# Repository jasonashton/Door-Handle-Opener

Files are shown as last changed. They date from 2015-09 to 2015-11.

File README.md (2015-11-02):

# Door-Handle-Opener

Opens a door handle with a Nema 17.  
**Problem:** In our residence hall, we can open the main doors with our ID cards but have to use a key to open the individual rooms.  
**Solution:** We've built a spool-and-motor system to open the door handle without altering the existing door.

##Parts List
1. Custom Built Microcontroller (heavily based on Arduino Uno) <em>see wiki</em>
2. A4988 Motor Driver (allows us to drive motors with independent power supply)
3. Nema 17 Stepper Motor
4. 3D Printed Parts <em>see models</em>

##Configuring the Motor Driver
The Motor Driver we chose to use is the Polulu A4988  
The Motor we chose is a Nema 17

To configure the current limiting on the motor driver, we use the formula
Current Limit = VREF x 2.5

Measure the voltage on the potentiometer (VREF). In Full Step mode, the driver will
only pull 70% of the current.

Current Limit / 2.5 = VREF

To get a full-step coil current of 1.4 Amps, the limit should be 1.4A/0.7 or 2
Amps. To find VREF, 2A/2.5 = .8 Volts. 

However, that might run a bit hot. Anything over 1 Amp requires external
cooling. To achieve a 1 Amp load,
1A/0.7 = 10/7A & 10/7A/2.5 = .572 Volts on VREF

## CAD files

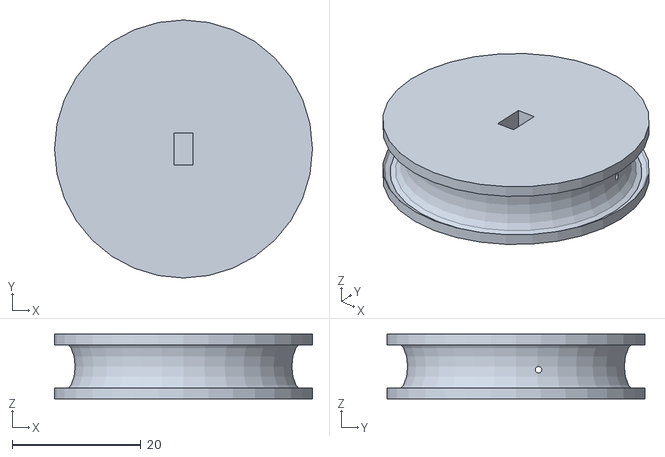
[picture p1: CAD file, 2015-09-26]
models/spool.stl
40.0 x 40.0 x 10.0

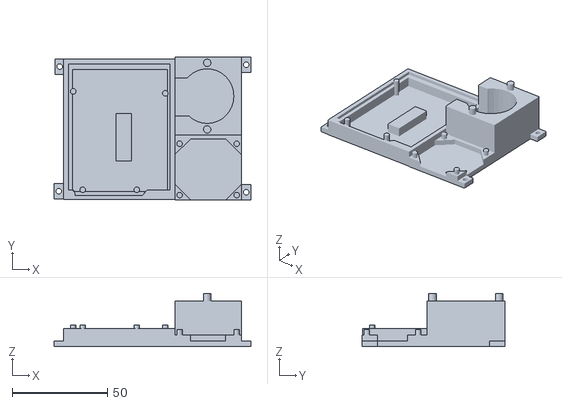
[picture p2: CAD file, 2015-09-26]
models/motorboard_mount.stl
103.5 x 75.0 x 28.0

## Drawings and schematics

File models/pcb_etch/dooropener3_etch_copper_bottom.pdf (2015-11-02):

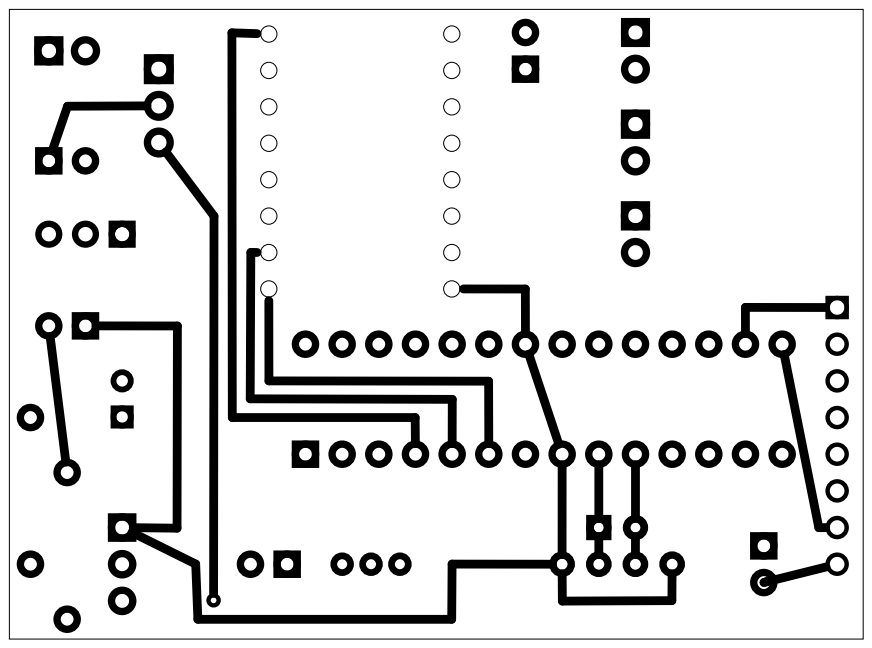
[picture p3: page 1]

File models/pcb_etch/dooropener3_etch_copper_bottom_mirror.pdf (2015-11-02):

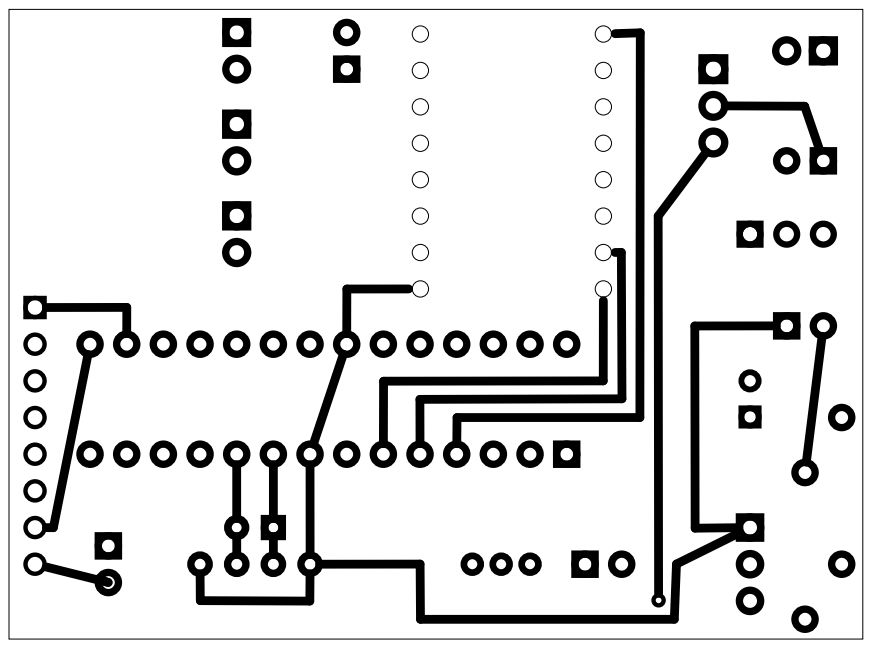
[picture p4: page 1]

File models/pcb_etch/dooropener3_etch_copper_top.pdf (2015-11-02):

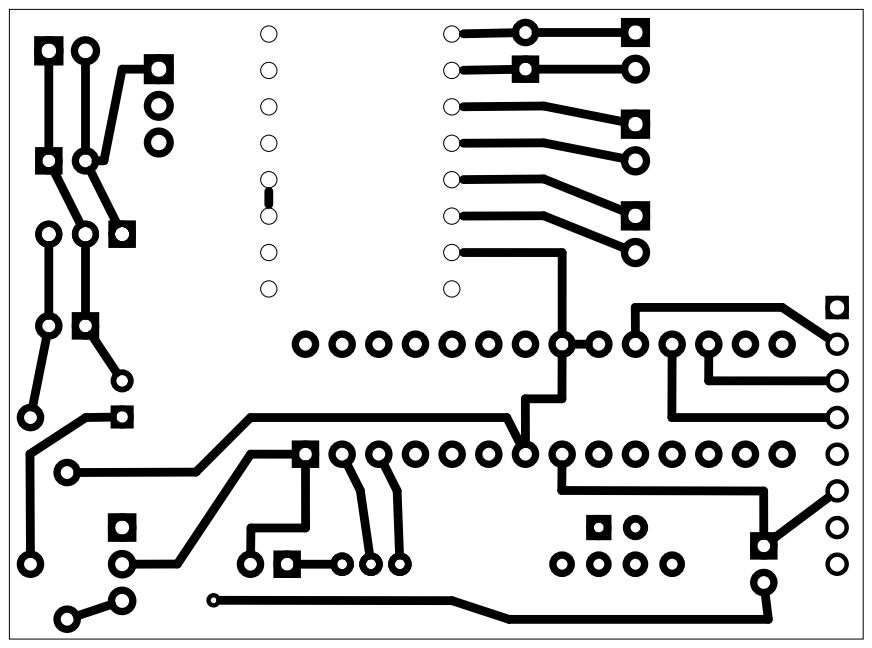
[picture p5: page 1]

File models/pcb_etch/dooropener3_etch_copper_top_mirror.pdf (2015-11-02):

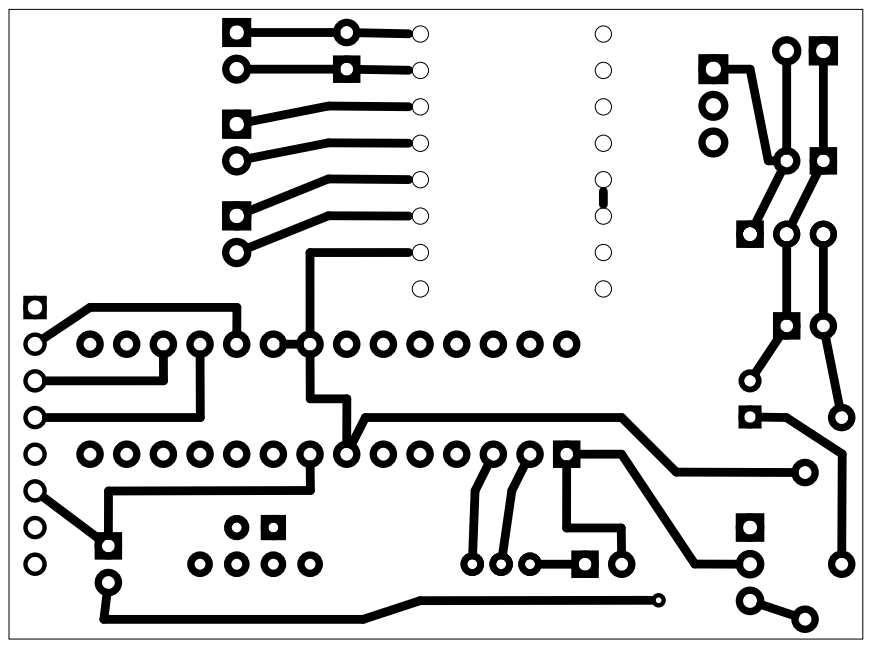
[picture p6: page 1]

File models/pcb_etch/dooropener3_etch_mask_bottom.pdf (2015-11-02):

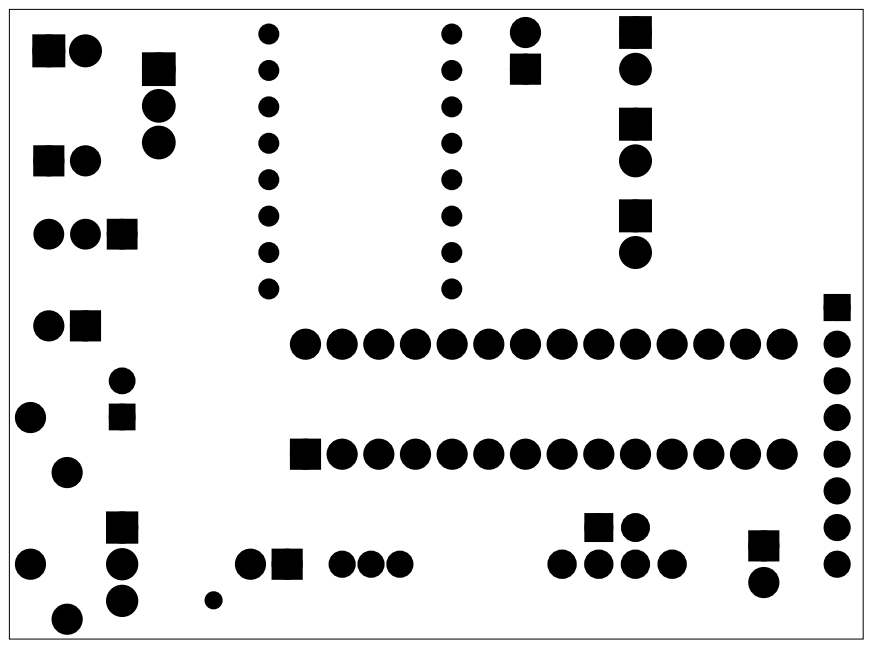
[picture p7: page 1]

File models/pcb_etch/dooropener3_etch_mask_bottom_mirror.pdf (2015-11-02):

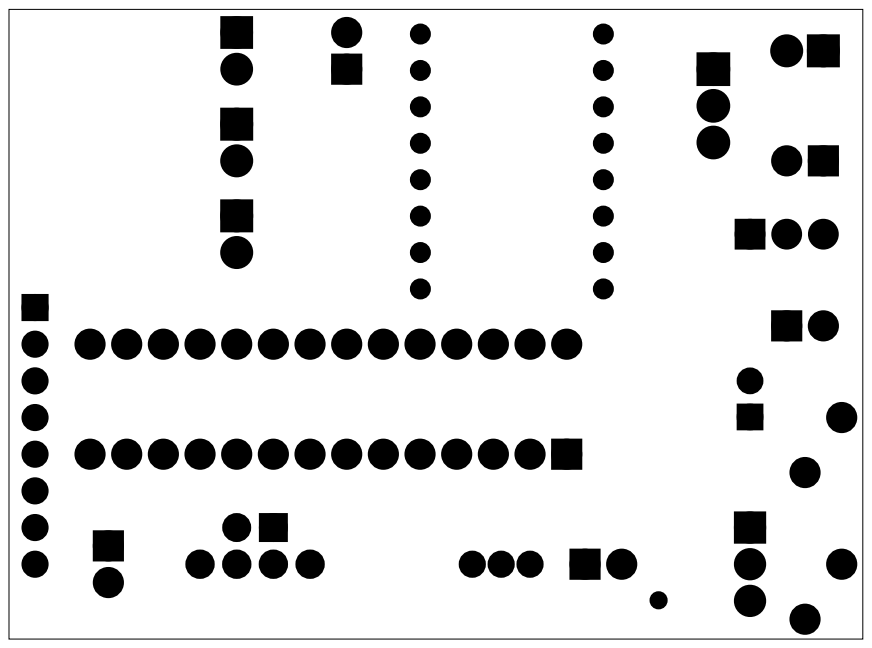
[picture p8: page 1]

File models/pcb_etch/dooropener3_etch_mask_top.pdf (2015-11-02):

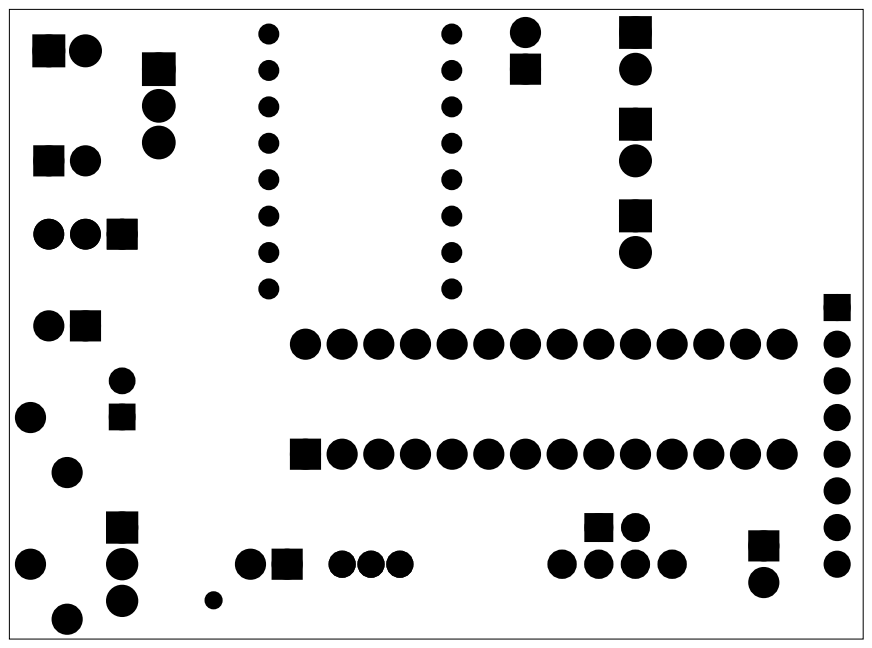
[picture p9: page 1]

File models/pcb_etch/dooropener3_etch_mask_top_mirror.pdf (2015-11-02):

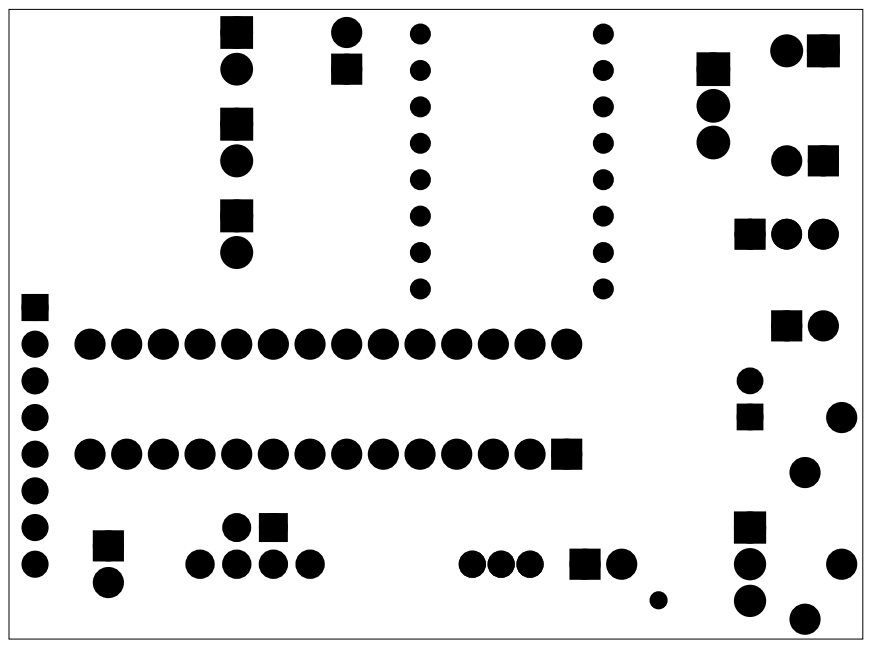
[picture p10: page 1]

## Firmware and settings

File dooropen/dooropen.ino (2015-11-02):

#include <SPI.h>
#include <MFRC522.h>

//CardReader Constants
#define RST_PIN 9 
#define SS_PIN 10

//Motor Drive Contants
#define ENABLE_PIN 2
#define STEP_PIN 3
#define DIR_PIN 4

String cards[2] = {"15318785229", "103113543"}; //Accepted Keys
byte cardread[4]; //To store read key

//CardReader Initialize
MFRC522 mfrc522(SS_PIN, RST_PIN);   // Create MFRC522 instance.
MFRC522::MIFARE_Key key;

void setup(){
  Serial.begin(9600);
  pinMode(ENABLE_PIN,OUTPUT); // Enable
  pinMode(STEP_PIN,OUTPUT); // Step
  pinMode(DIR_PIN,OUTPUT); // Dir
  digitalWrite(ENABLE_PIN,HIGH); // Set Enable off
  
  SPI.begin();        // Init SPI bus
  mfrc522.PCD_Init(); // Init MFRC522 card
  mfrc522.PCD_SetAntennaGain(mfrc522.RxGain_max); //Set Max Gain ?working?
}

void loop() {
  // Look for new cards
    if ( ! mfrc522.PICC_IsNewCardPresent())
        return;
        
    // Select one of the cards
    if ( ! mfrc522.PICC_ReadCardSerial())
        return;
    
    dump_byte_array(mfrc522.uid.uidByte, mfrc522.uid.size); //card to cardread


    //If they're the same print match
    if(compare_arrays(cards, cardread)){
      motorDrive();
    }
    
    
}

/**
 * Helper routine to dump a byte array as hex values to Serial.
 */
void dump_byte_array(byte *buffer, byte bufferSize) {
    for (byte i = 0; i < bufferSize; i++) {
        cardread[i] = buffer[i];
    }
}

/**
 * Compares two cards
 */
boolean compare_arrays(String master[], byte readcard[]){
  String card_to_string;

  //convert the read uid to a string
  for(byte i=0;i<4;i++){
    card_to_string += readcard[i];
  }
  
  //return true if they match, cycles through each available "correct" card
  for(byte i=0;i<2;i++){
    if(master[i] == card_to_string){
      return true;
    }
  }
   return false;
}

void motorDrive(){
  digitalWrite(ENABLE_PIN, LOW);
  digitalWrite(DIR_PIN, HIGH);
    
  for(int i=0; i<=200; i++){
    digitalWrite(STEP_PIN,HIGH); // Output high
    delay(5); // Wait
    digitalWrite(STEP_PIN,LOW); // Output low
    delay(5); // Wait
  }
  
  digitalWrite(DIR_PIN, LOW);
  
  for(int i=0; i<=200; i++){
    digitalWrite(STEP_PIN,HIGH); // Output high
    delay(5); // Wait
    digitalWrite(STEP_PIN,LOW); // Output low
    delay(5); // Wait
  }
  
  digitalWrite(ENABLE_PIN, HIGH);
  }

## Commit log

2015-09-26 Uploaded .stl's
    [motorboard_mount.stl, spool.stl]
2015-09-26 moved files
    [motorboard_mount.stl, spool.stl]
2015-10-10 included required libraries and deleted old motor drive code
2015-10-11 Added Fritzing Models
    [dooropener.fzz, dooropener3.fzz, dooroperner2.fzz]
2015-10-11 Removed Old Motor Driver Code
2015-10-15 added pcb
    [dooropener3.fzz]
2015-10-18 Final PCB design
    [dooropener3.fzz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]
2015-11-02 working motor drive
